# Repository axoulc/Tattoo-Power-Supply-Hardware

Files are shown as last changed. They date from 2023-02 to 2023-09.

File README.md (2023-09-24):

# Tattoo Power Supply Hardware

 

<p align="center">
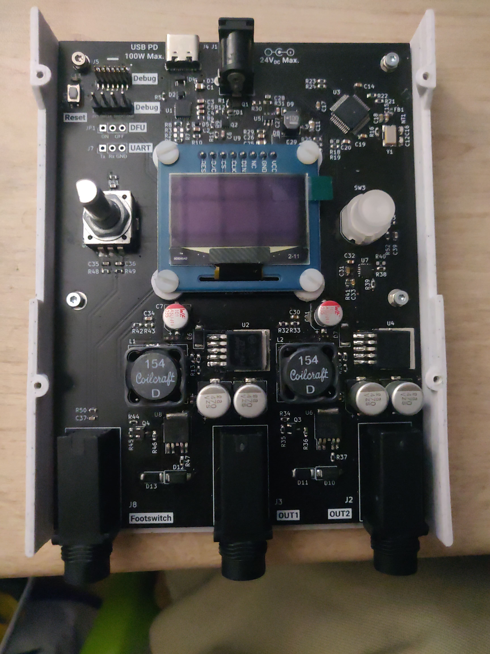
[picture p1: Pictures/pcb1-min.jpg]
    
</p>

This is an open source project for a tattoo power supply circuit board. The circuit board is designed to provide power to tattoo machines, allowing artists to control the voltage and frequency of their machines for precise and consistent results.

# Features

- Dual channel power supply
- Each channel can provide up to 20V and 3A
- 1 footswitch input and 1 handswitch input
- Adjustable voltage and frequency controls
- Compatible with most tattoo machines
- OLED display for easy monitoring of voltage and frequency
- Overload protection for safety
- USB-C Power Delivery up to 100W
- DC Jack input up to 24V

# Getting Started

## PCB

To get started with this project, you will need at least KiCAD 7. You can download KiCAD from the [KiCAD website](https://kicad.org/). You will find gerber files in each release, which you can use to order PCBs from a PCB manufacturer. Every files will be available in the PCB folder. For components, you can use the BOM file to order them from a distributor `Tattoo_Supply_bom_Vx.x.csv`.

## Case

<p align="center">
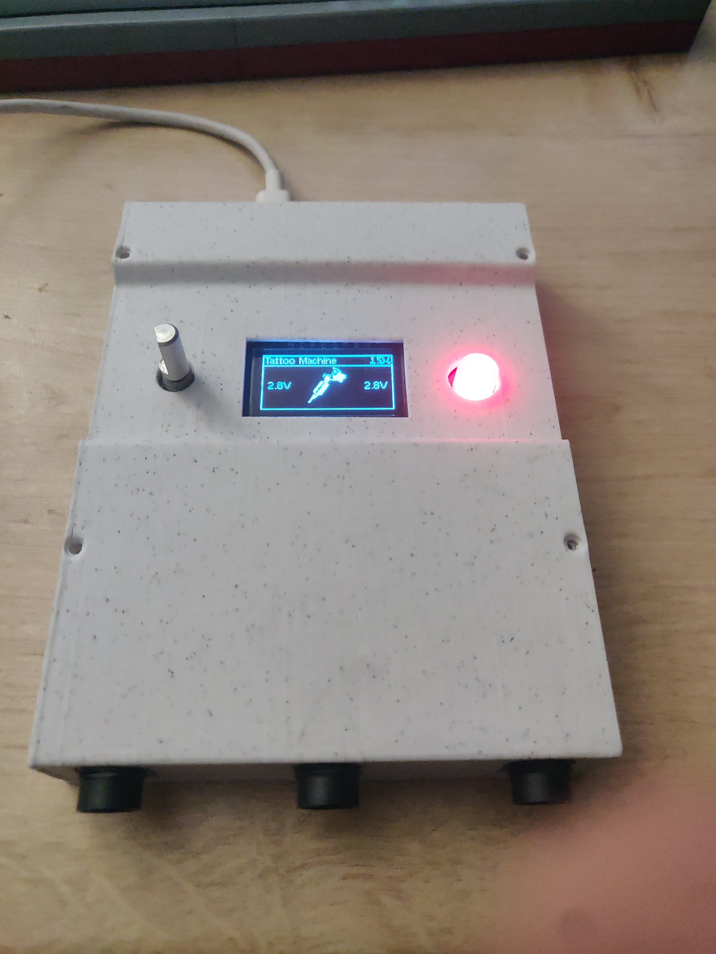
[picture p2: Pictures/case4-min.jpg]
    
</p>

The case is designed with FreeCAD. In `Case` folder, you will find `.FCStd` files which are source files for FreeCAD and `.3mf` files which are 3D printer ready. The shapes of the case are very simple, if you're 3D designer, make it prettier !

# License

This project is licensed under the CERN Open Hardware Licence Version 2 - Permissive. See the LICENSE file for more information.

# Contact

If you have any questions or feedback about this project, please feel free to contact the project maintainer in issue section.

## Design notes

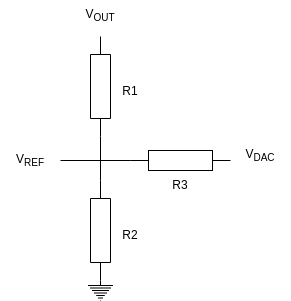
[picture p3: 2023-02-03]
PCB/notebook/img/smps_feedback.drawio.png

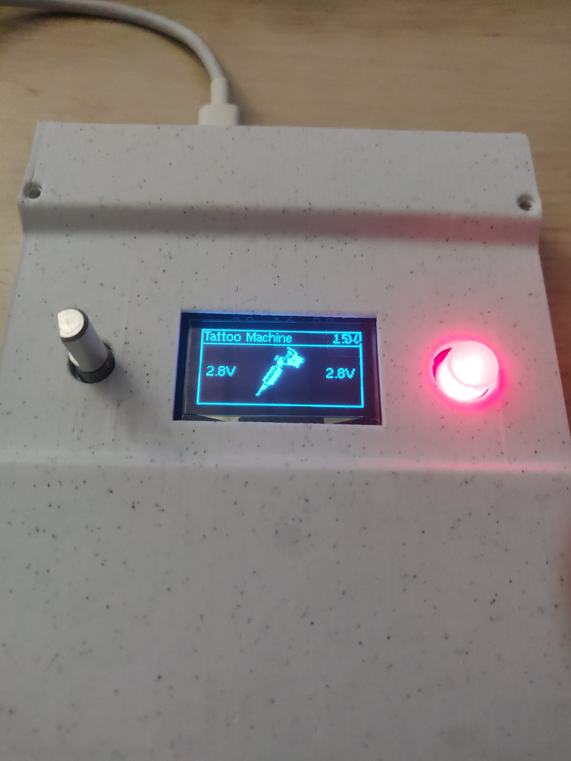
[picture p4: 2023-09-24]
Pictures/case3-min.jpg

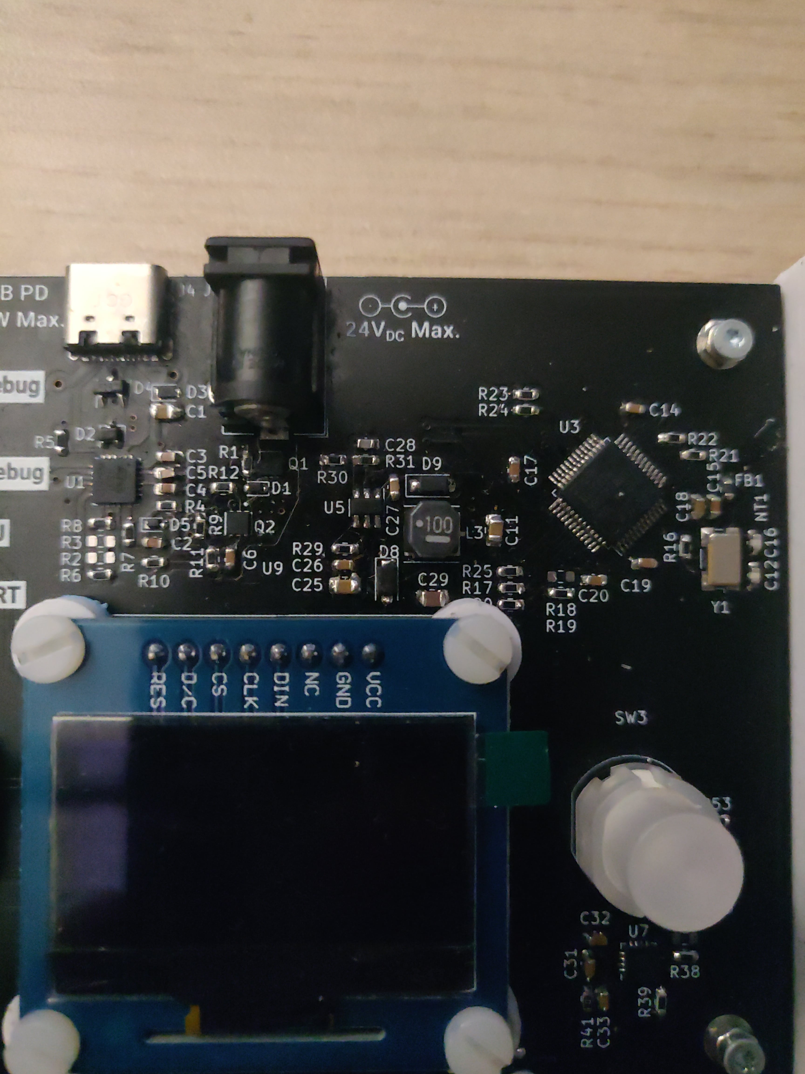
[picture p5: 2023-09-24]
Pictures/pcb3-min.jpg

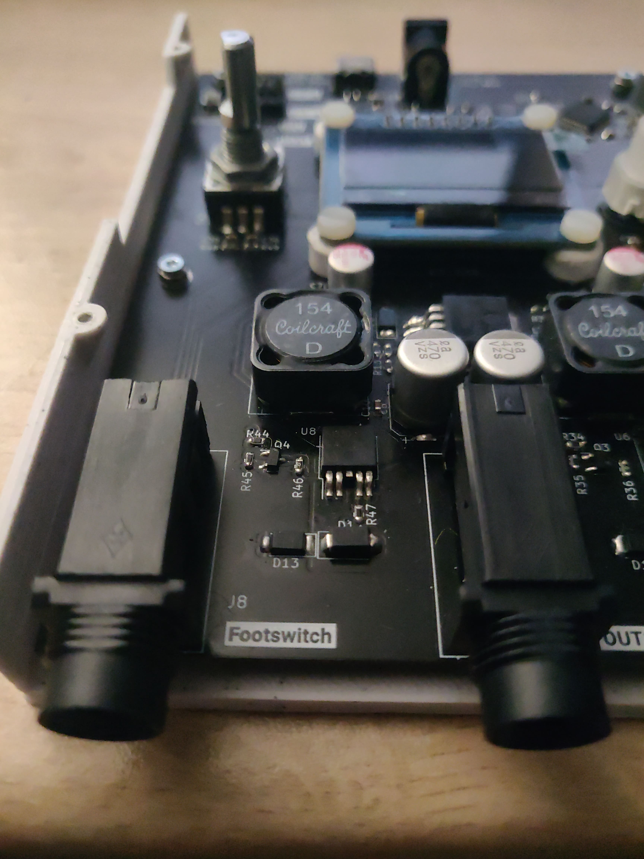
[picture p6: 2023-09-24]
Pictures/pcb2-min.jpg

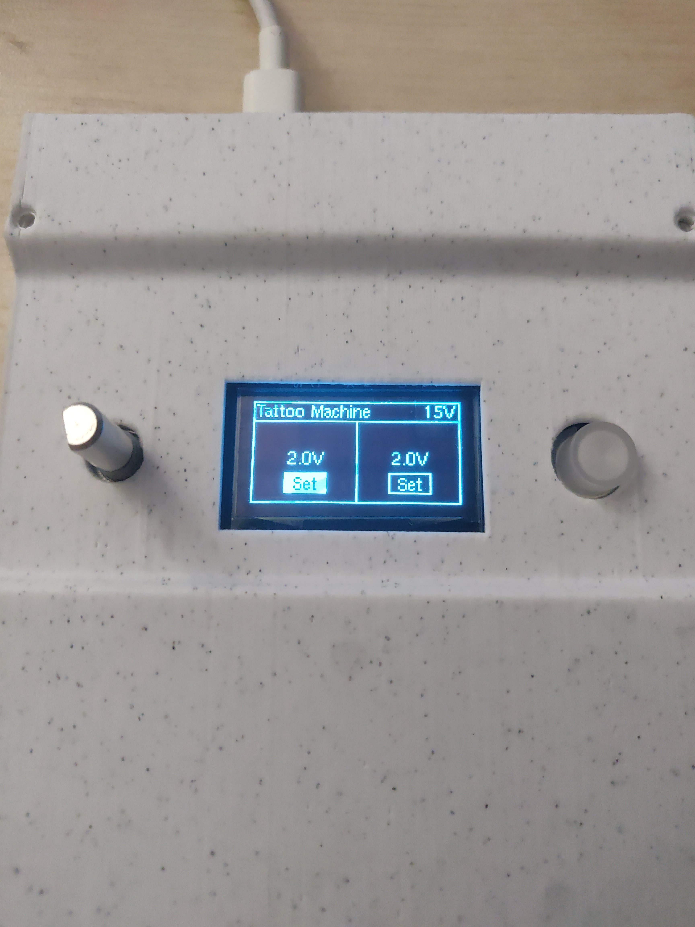
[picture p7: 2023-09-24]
Pictures/case2-min.jpg

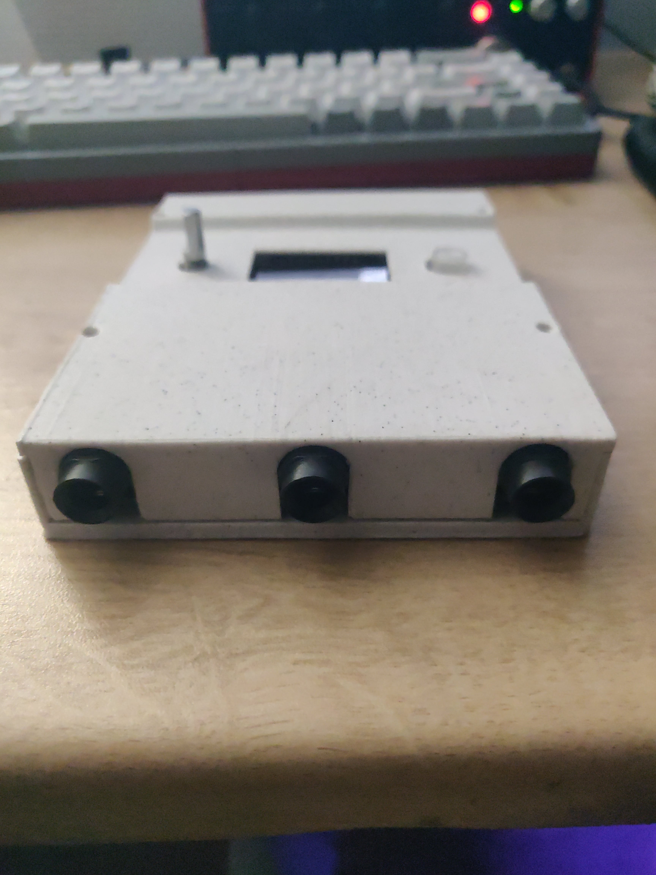
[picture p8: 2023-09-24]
Pictures/case1-min.jpg

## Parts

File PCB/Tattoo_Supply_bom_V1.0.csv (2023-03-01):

References | Value | Footprint | Quantity Per PCB | Manufacturer | MPN | Alt Manufacturer | Alt MPN
C12 C16 | 20p | C_0603_1608Metric | 2 | Kemet | C0603C200J5HACTU
C28 | 47p | C_0603_1608Metric | 1 | TDK | C1608C0G1H470J080AA
C18 C35 C36 C37 C38 C39 | 10n | C_0603_1608Metric | 6 | Murata | GCM188R71H103KA37J
C6 C13 C14 C17 C19 C20 C26 C27 C31 C33 | 100n | C_0603_1608Metric | 10 | TDK | CGA3E2X7R1H104M080AA
C2 C3 C4 C5 C10 C15 C24 C30 C34 | 1u | C_0603_1608Metric | 9 | TDK | CGA3E1X7R1V105K080AC
C32 | 1.5u | C_0603_1608Metric | 1 | TDK | C1608X7R1A155K080AC
C1 C11 C25 | 4.7u | C_0805_2012Metric | 3 | Murata | GRM219R6YA475KA73D
C29 | 22u | C_0805_2012Metric | 1 | Murata | GRM21BC81C226ME44L
C7 C21 | 100u/35V | CP_Elec_6.3x7.7 | 2 | Wurth Elektronik | 865080545012
C8 C9 C22 C23 | 470u/35V | CP_Elec_8x10 | 4 | United Chemi-Con | EMZS350ARA471MHA0G
D9 | 1N4148W | D_SOD-123 | 1 | Diodes Incorporated | 1N4148W-7-F
D10 D12 | 1SMA5936BT3G | D_SMA | 2 | Onsemi | 1SMA5936BT3G
D1 | BZX585-B10 | D_SOD-523 | 1 | Nexperia | BZX585-B10,135
D3 | ESDA25P35 | D_0603_1608Metric | 1 | STMicroelectronics | ESDA25P35-1U1M
D2 | ESDA25W | SOT-323_SC-70 | 1 | STMicroelectronics | ESDA25W
D4 | PACDN042Y3R | SOT-23-3 | 1 | Onsemi | PACDN042Y3R
D6 D7 | PMEG4050EP,115 | D_SOD-128 | 2 | Nexperia | PMEG4050EP,115
D8 | PMEG6010ER,115 | D_SOD-123F | 1 | Nexperia | PMEG6010ER,115
D5 | RB501SM-30FHT2R | D_SOD-523 | 1 | ROHM | RB501SM-30FHT2R
D11 D13 | RF202LAM2STR | D_SOD-128 | 2 | ROHM | RF202LAM2STR
FB1 | 600/100MHz | R_0603_1608Metric | 1 | Wurth Elektronik | 742792651
J1 | Barrel_Jack_Switch | BarrelJack_CUI_PJ-102AH_Horizontal | 1 | CUI Devices | PJ-102A
J5 | Conn_ST_STDC14 | PinSocket_2x07_P1.27mm_Vertical_SMD | 1 | Amphenol FCI | 20021121-00014C1LF
J2 J3 J8 | Out_{1} Out_{2} Footswitch | MJ63022A | 3 | CUI Devices | MJ-63022A
J4 | USB_C_Receptacle_USB2.0 | USB_C_Receptacle_GCT_USB4105-xx-A_16P_TopMnt_Horizontal | 1 | GCT | USB4105-GF-A
L1 L2 | MSS1583-154KED | MSS1583 | 2 | Coilcraft | MSS1583-154KED
L3 | NRS5040T100MMGJ | L_Taiyo-Yuden_NR-50xx | 1 | Taiyo Yuden | NRS5040T100MMGJ
Q3 Q4 | 2N7002 | SOT-23 | 2 | Nexperia | 2N7002NXAKR
Q2 | SSM6J507NU | TRANS_SSM6J507NU,LF | 1 | Toshiba | SSM6J507NU,LF
Q1 | SiA441DJ | Vishay_PowerPAK_SC70-6L_Single | 1 | Vishay Semiconductors | SIA441DJ-T1-GE3
R36 R46 | 0 | R_0603_1608Metric | 2 | Panasonic | ERJ-3GEY0R00V
R23 R24 | 20 | R_0603_1608Metric | 2 | Panasonic | ERJ-3EKF20R0V
R34 R44 | 22 | R_0603_1608Metric | 2 | Panasonic | ERJ-3EKF22R0V
R11 | 100 | R_0603_1608Metric | 1 | Panasonic | ERJ-3EKF1000V
R4 | 470 | R_0603_1608Metric | 1 | Panasonic | ERJ-3EKF4700V
R16 | 953 | R_0603_1608Metric | 1 | Panasonic | ERJ-3EKF9530V
R7 R12 R14 R27 R37 R47 R53 | 1k | R_0603_1608Metric | 7 | Panasonic | ERJ-3EKF1001V
R33 R43 | 1.62k | R_0603_1608Metric | 2 | Panasonic | ERJ-3EKF1621V
R15 R28 | 1.65k | R_0603_1608Metric | 2 | Panasonic | ERJ-3EKF1651V
R17 R20 | 4.7k | R_0603_1608Metric | 2 | Panasonic | ERJ-3EKF4701V
R13 R26 | 8.45k | R_0603_1608Metric | 2 | Panasonic | ERJ-3EKF8451V
R21 R35 R38 R39 R41 R45 R48 R49 R50 R51 R52 | 10k | R_0603_1608Metric | 11 | Panasonic | ERJ-3EKF1002V
R32 R42 | 13.3k | R_0603_1608Metric | 2 | Panasonic | ERJ-3EKF1332V
R10 | 18k | R_0603_1608Metric | 1 | Panasonic | ERJ-3EKF1802V
R30 | 40.2k | R_0603_1608Metric | 1 | Panasonic | ERJ-3EKF4022V
R1 R5 R6 R8 R9 R18 R19 R22 R25 | 100k | R_0603_1608Metric | 9 | Panasonic | ERJ-3EKF1003V
R31 | 124k | R_0603_1608Metric | 1 | Panasonic | ERJ-3EKF1243V
R29 | 499k | R_0603_1608Metric | 1 | Panasonic | ERJ-3EKF4993V
SW3 | Handswitch W LED | D6RLxx | 1 | C&K | D6RLRDF1 LFS
SW1 | Reset | SW_SPST_EVQP2 | 1 | Panasonic | EVQ-P2602W
SW2 | RotaryEncoder_Switch | RotaryEncoder_Alps_EC11E-Switch_Vertical_H20mm | 1 | Bourns | PEC11R-4220F-S0024
U6 U8 | BTS6133D | TO-252-4 | 2 | Infineon | BTS6133D
U7 | DACx3202 | WQFN-16-1EP_3x3mm_P0.5mm_EP1.68x1.68mm | 1 | Texas Instruments | DAC63202RTER
U2 U4 | LM2576S-ADJ | TO-263-5_TabPin3 | 2 | Onsemi | LM2576D2T-ADJR4G
U5 | MP2456 | TSOT-23-6 | 1 | Monolithic Power Systems | MP2456GJ-Z
U9 | OLED_Waveshare | OLEDs_Waveshare_4SPI | 1 | 10451 | Waveshare | Waveshare | 9092
U3 | STM32F103C8Tx | LQFP-48_7x7mm_P0.5mm | 1 | STMicroelectronics | STM32F103C8T6
U1 | STUSB4500QTR | QFN-24-1EP_4x4mm_P0.5mm_EP2.7x2.7mm | 1 | STMicroelectronics | STUSB4500QTR
Y1 | ABM3B-8.000MHZ-B2-T | Crystal_SMD_Abracon_ABM3B-4Pin_5.0x3.2mm | 1 | Abracon | ABM3B-8.000MHZ-B2-T

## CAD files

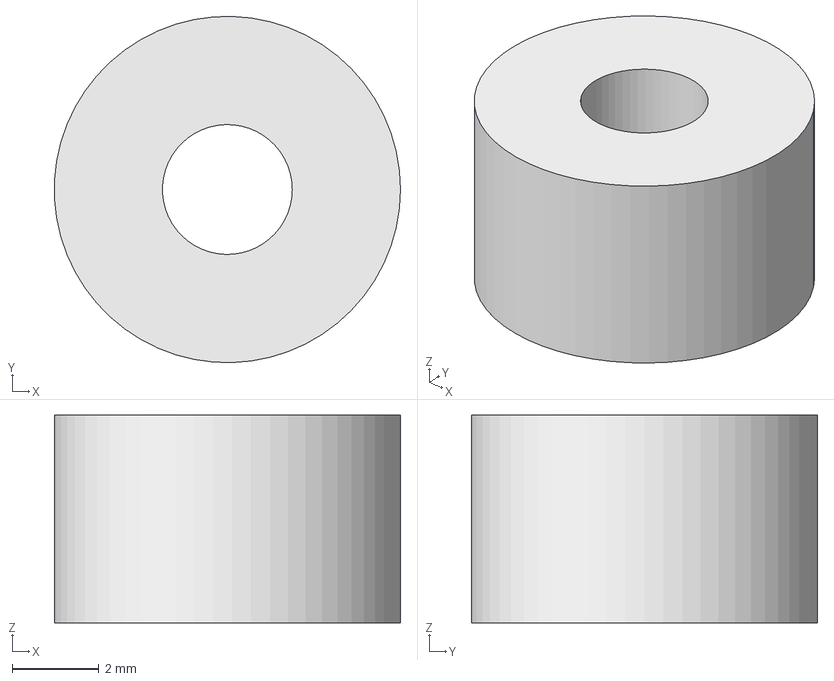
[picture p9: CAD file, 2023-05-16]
Case/oled_spacers.FCStd
7.99 x 8.00 x 4.80 mm

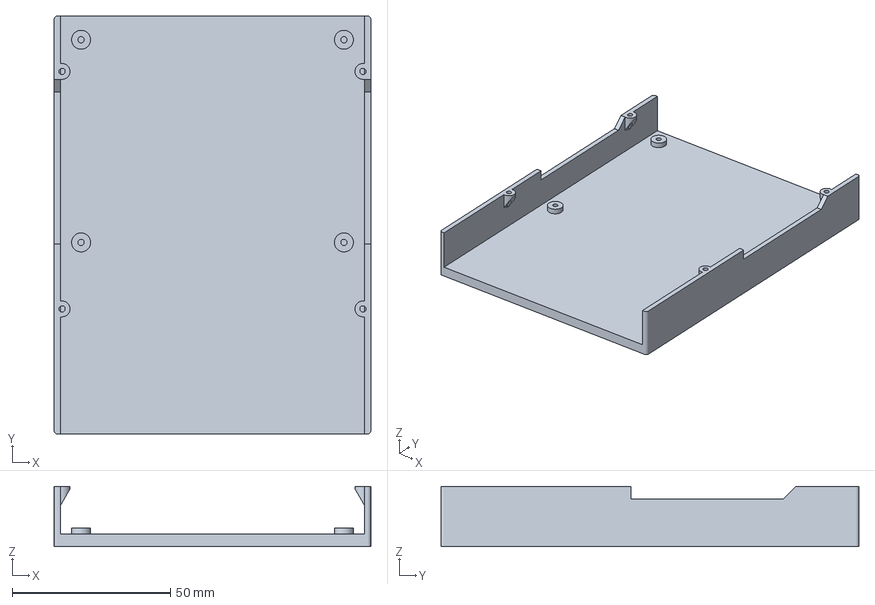
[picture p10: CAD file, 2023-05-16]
Case/Case_V1_bottom.3mf
100.0 x 132.0 x 19.0 mm

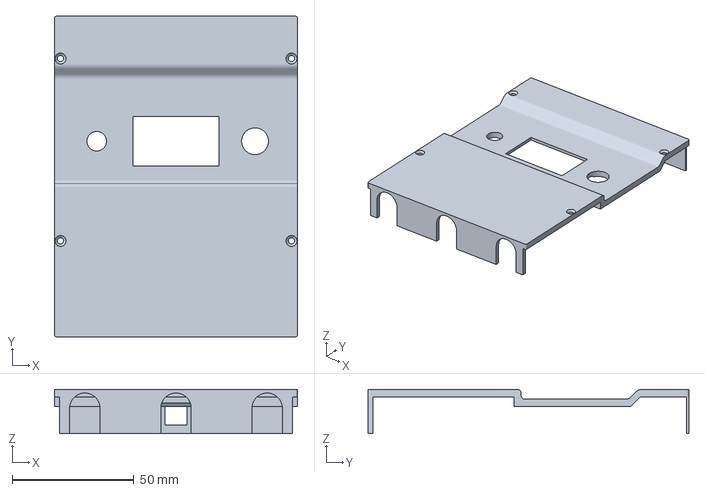
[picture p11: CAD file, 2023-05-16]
Case/Case_V1_top.3mf
100.0 x 132.0 x 18.1 mm

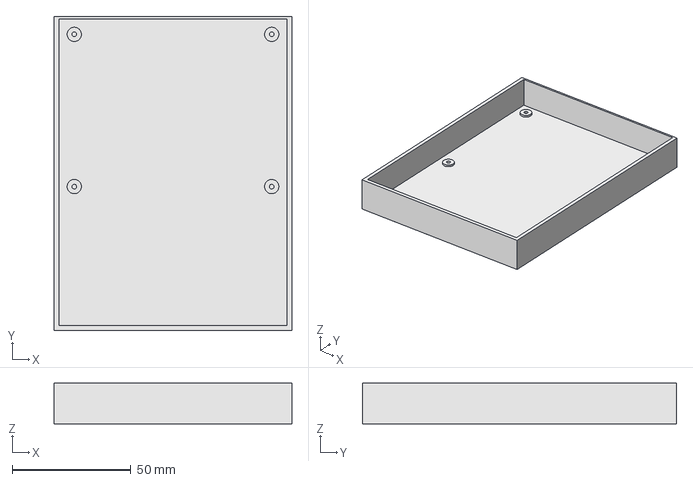
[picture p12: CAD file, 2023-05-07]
Case/Case_V1.0.FCStd
100.0 x 132.0 x 17.1 mm

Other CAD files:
Case/Oled_Spacers.3mf

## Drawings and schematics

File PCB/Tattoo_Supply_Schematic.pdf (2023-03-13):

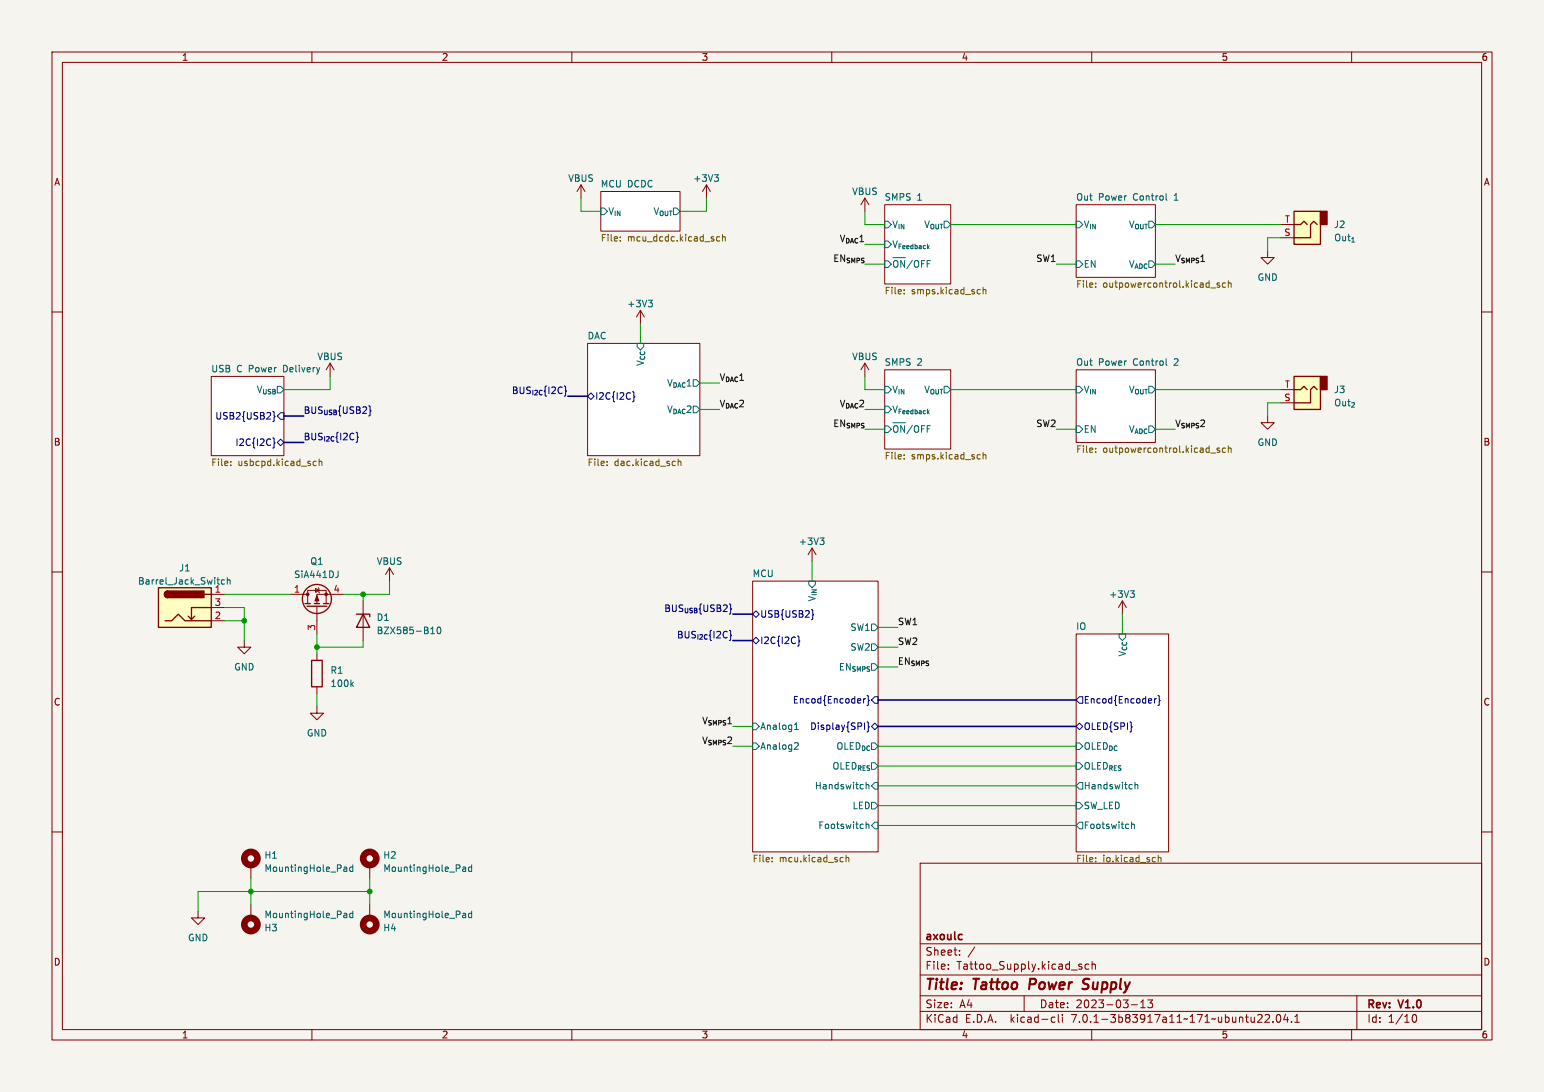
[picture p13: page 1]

~{ON}/OFF SMPS 1 File: smps.kicad_sch

VBUS
~{ON}/OFF SMPS 2 File: smps.kicad_sch
LED MCU

Encod{Encoder} V_{CC} Footswitch Handswitch OLED{SPI}

Id: 1/10 Title: Tattoo Power Supply

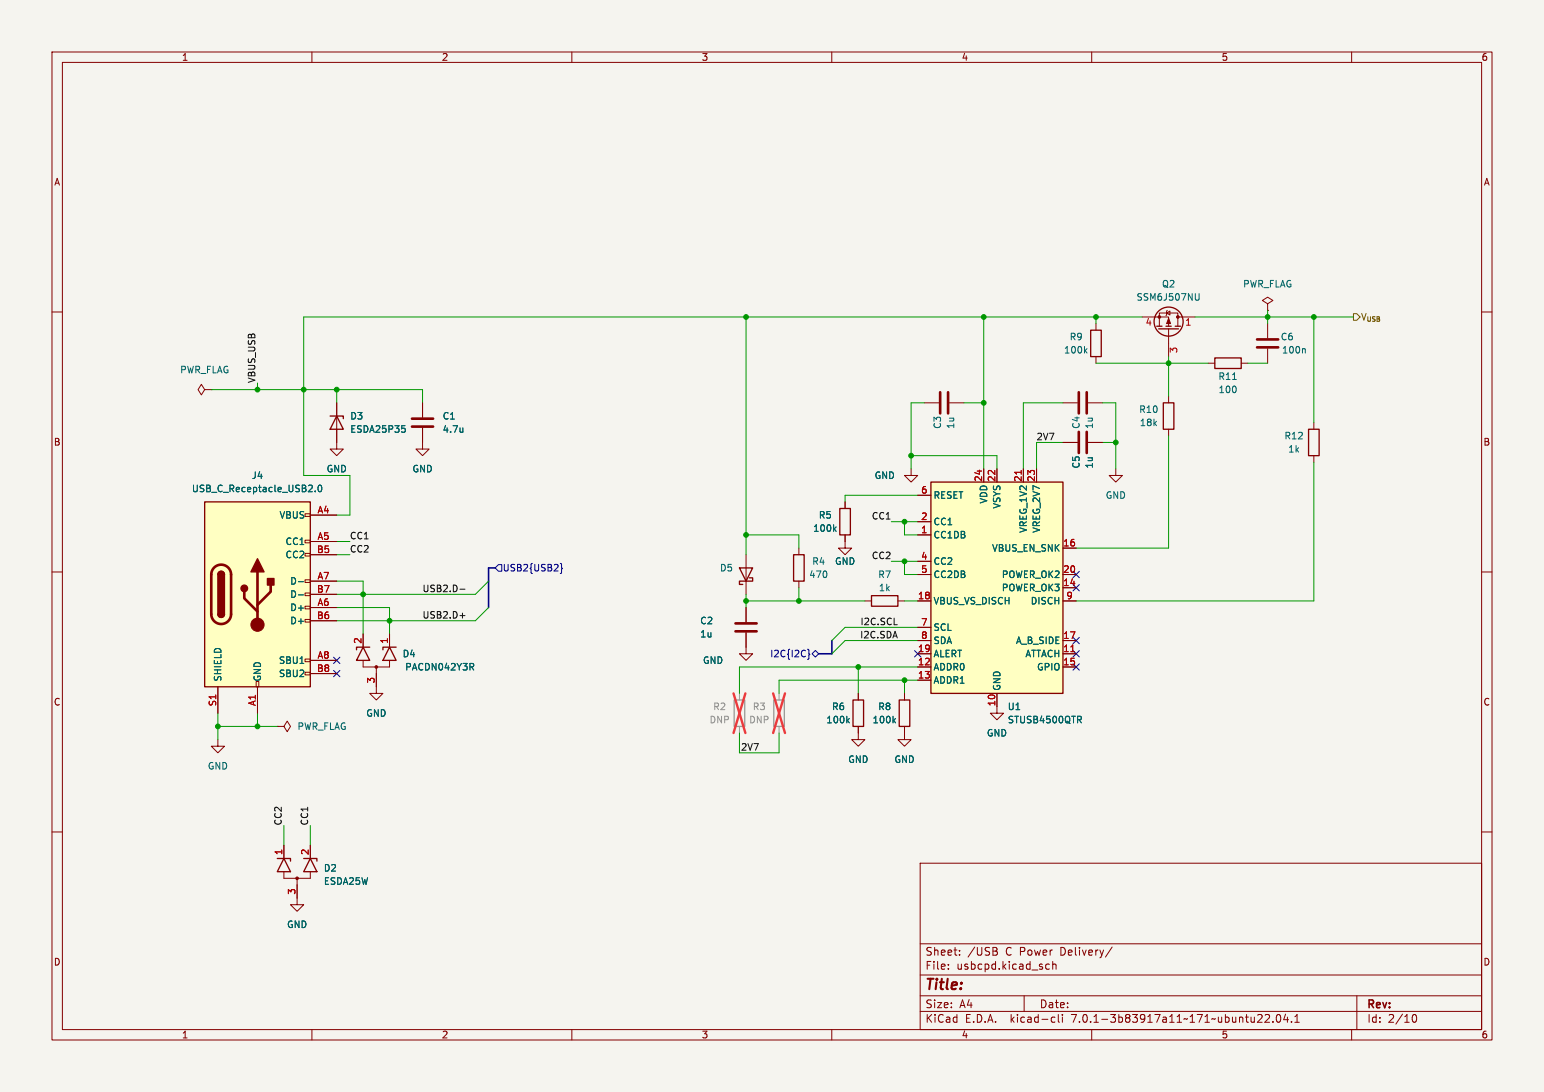
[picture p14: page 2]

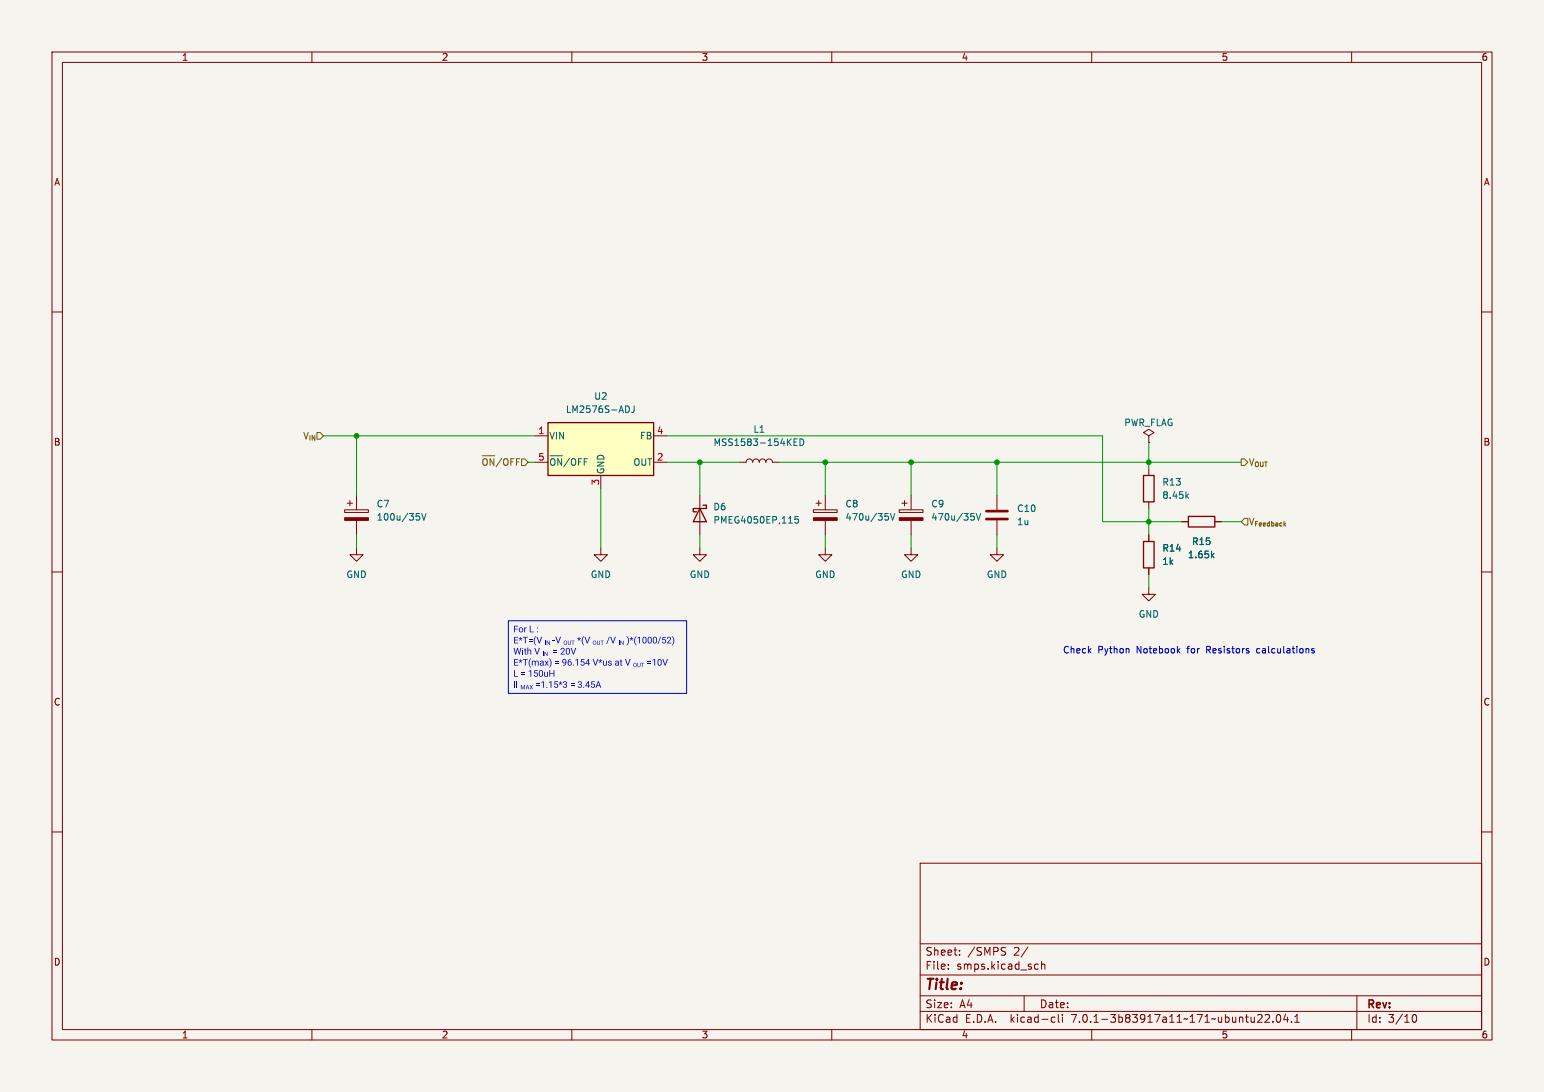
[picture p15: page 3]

Id: 3/10 Title: File: smps.kicad_sch Sheet: /SMPS 2/ C9

E*T(max) = 96.154 V*us at V _{OUT} =10V

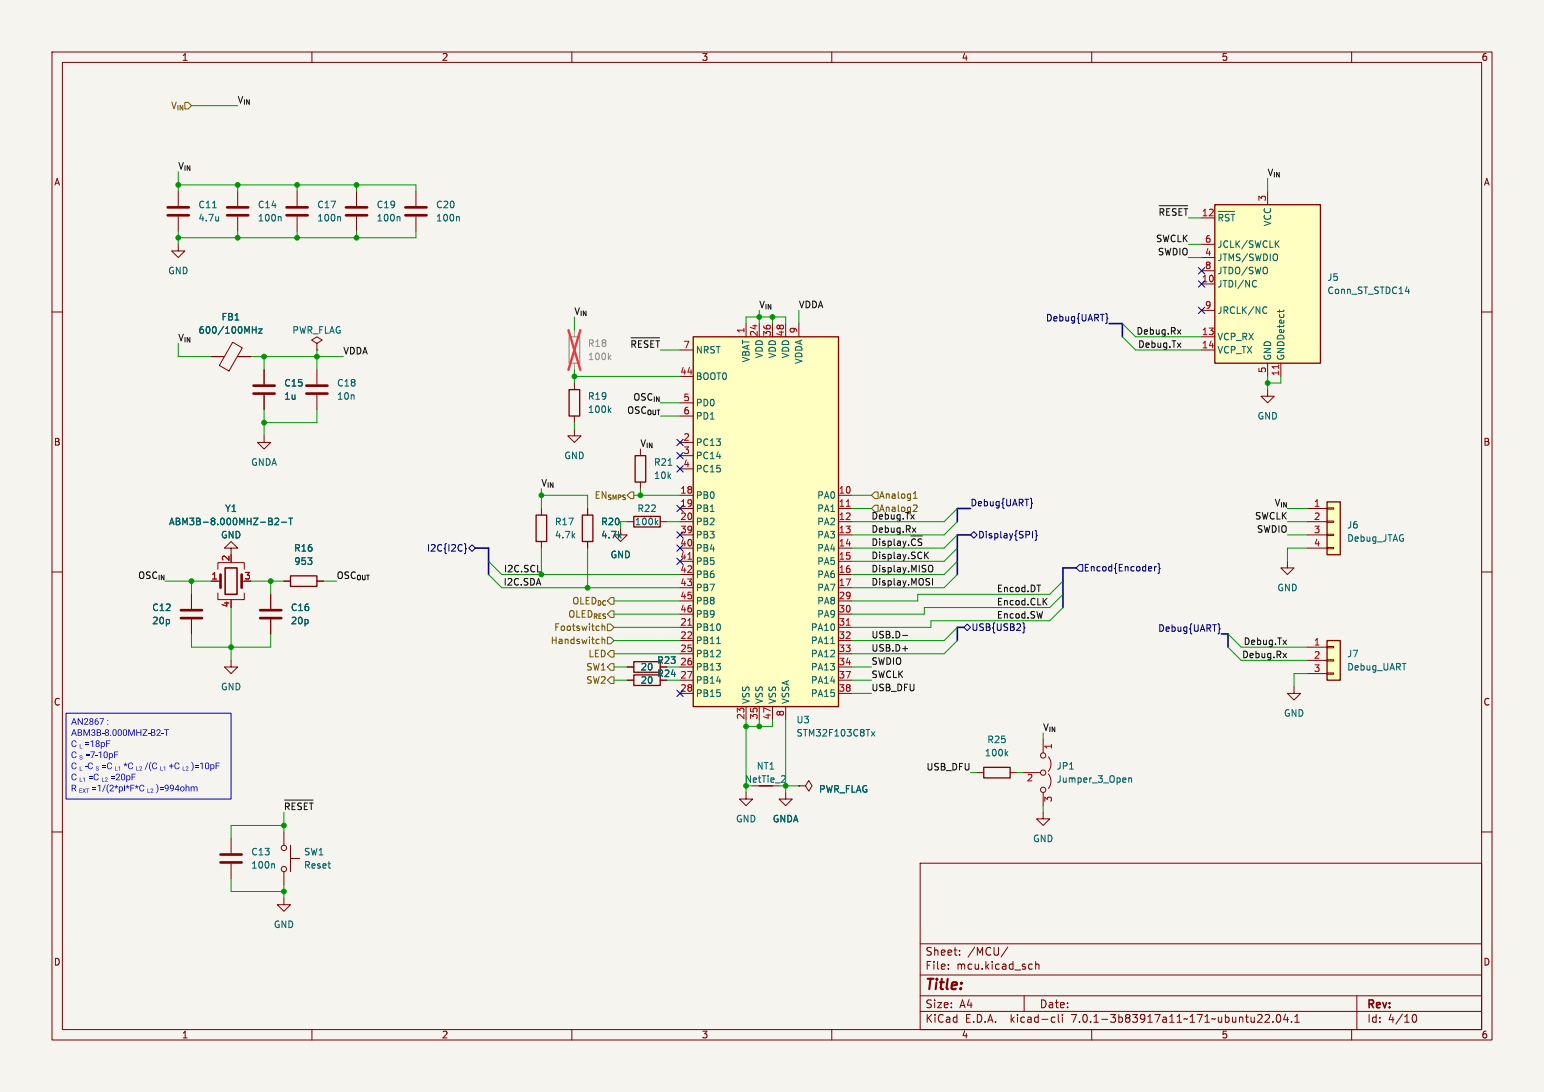
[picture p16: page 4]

1 PA0 10 PA1 11 PA2 12 PA3 13 PA4 14 PA5 15 PA6 16 PA7 17 PB0 18 PB1 19 PC13 2 PB2 20 PB10 21 PB11 22 VSS 23 VDD 24 PB12 25 PB13 26 PB14 27 PB15 28 PA8 29 PC14 3 PA9 30 PA10 31 PA11 32 PA12 33 PA13 34 VSS 35 VDD 36 PA14 37 PA15 38 PB3 39 PC15 4 PB4 40 PB5 41 PB6 42 PB7 43 BOOT0 44 PB8 45 PB9 46 VSS 47 VDD 48 PD0 5 PD1 6 NRST 7 VSSA

Id: 4/10 Title: File: mcu.kicad_sch Sheet: /MCU/ R23

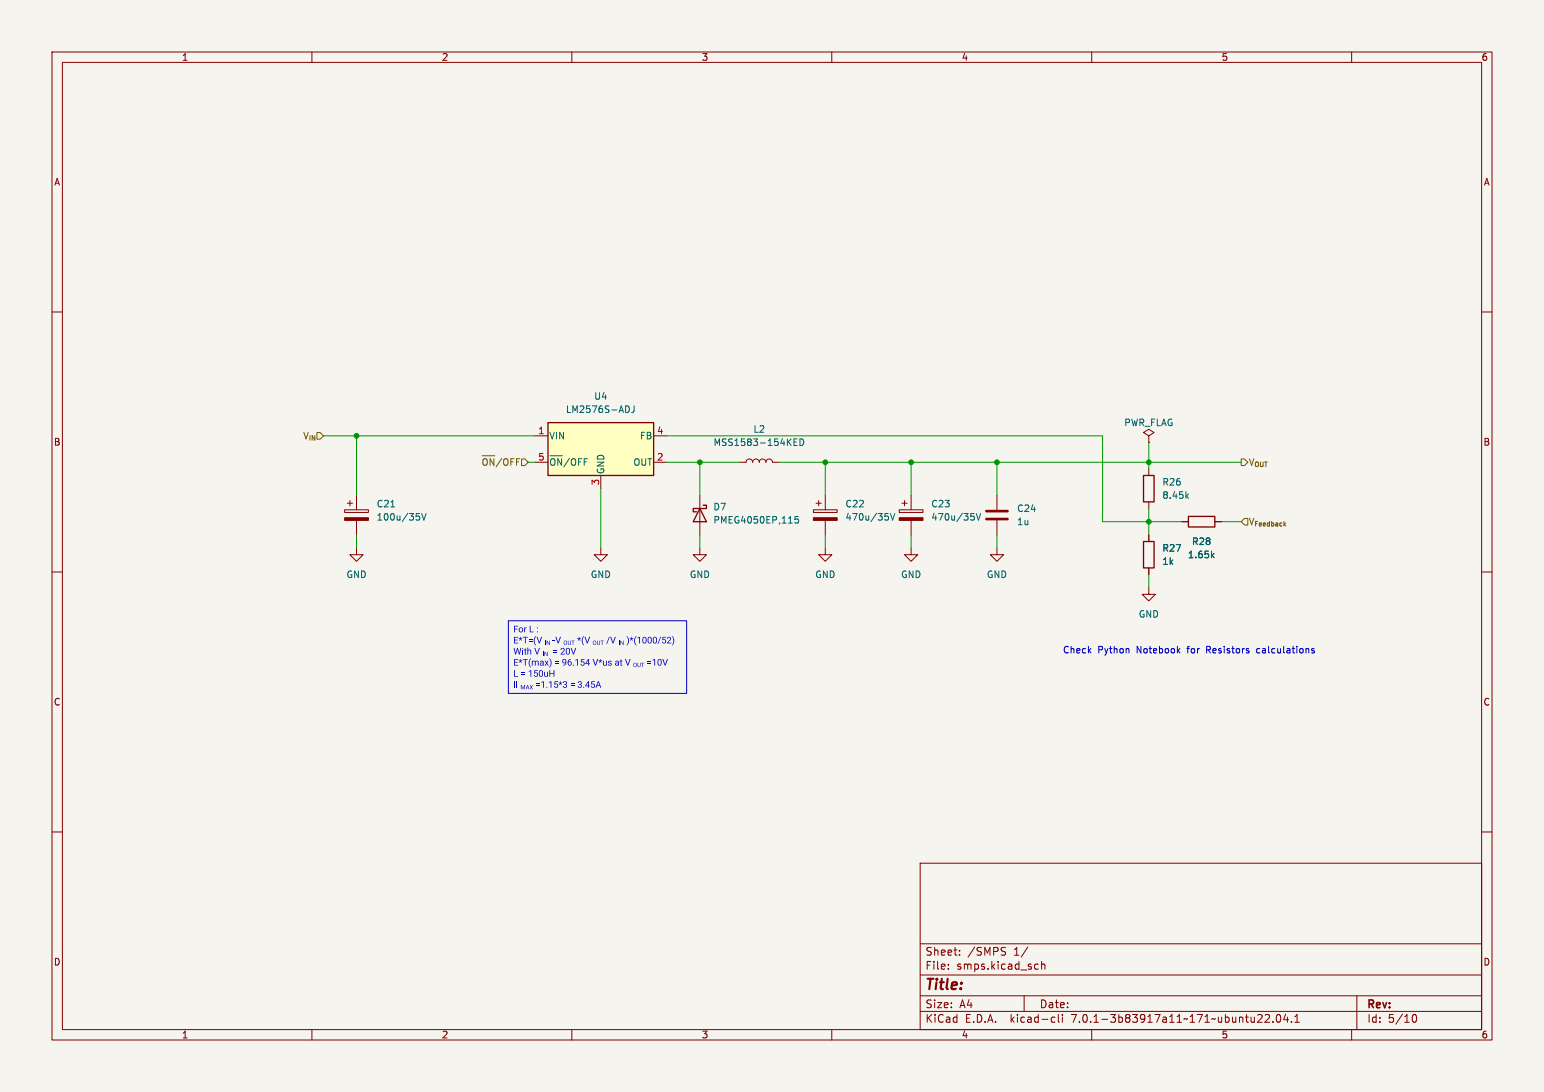
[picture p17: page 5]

Id: 5/10 Title: File: smps.kicad_sch Sheet: /SMPS 1/ C22

E*T(max) = 96.154 V*us at V _{OUT} =10V

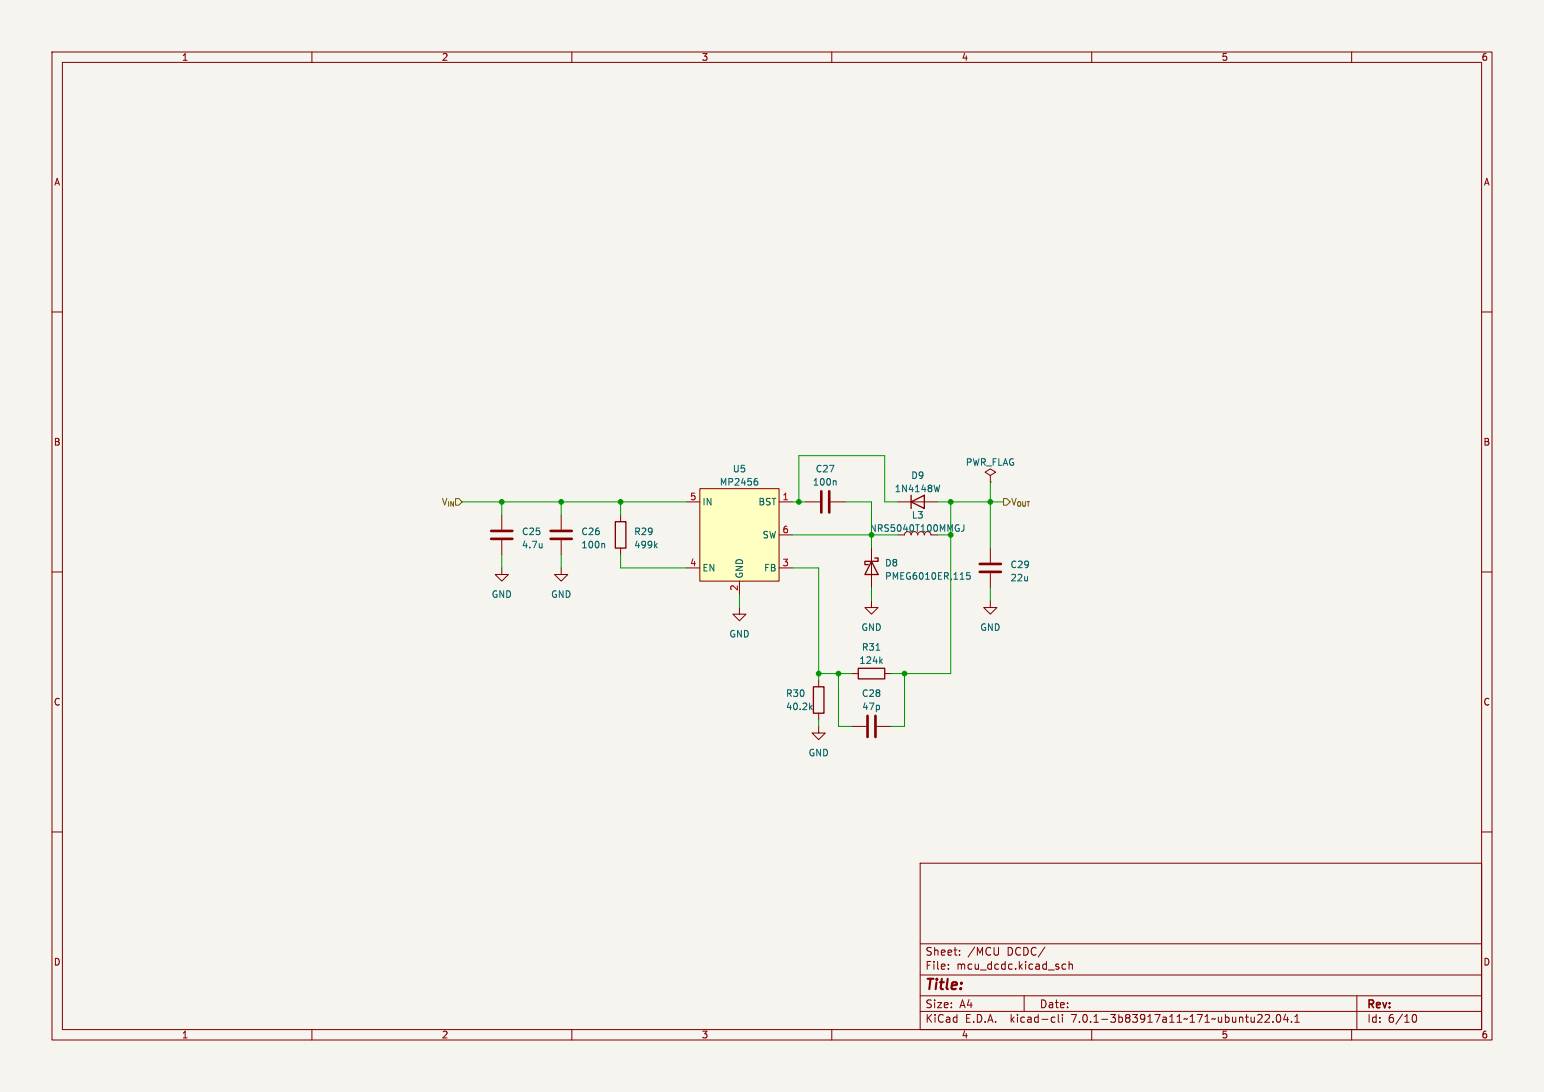
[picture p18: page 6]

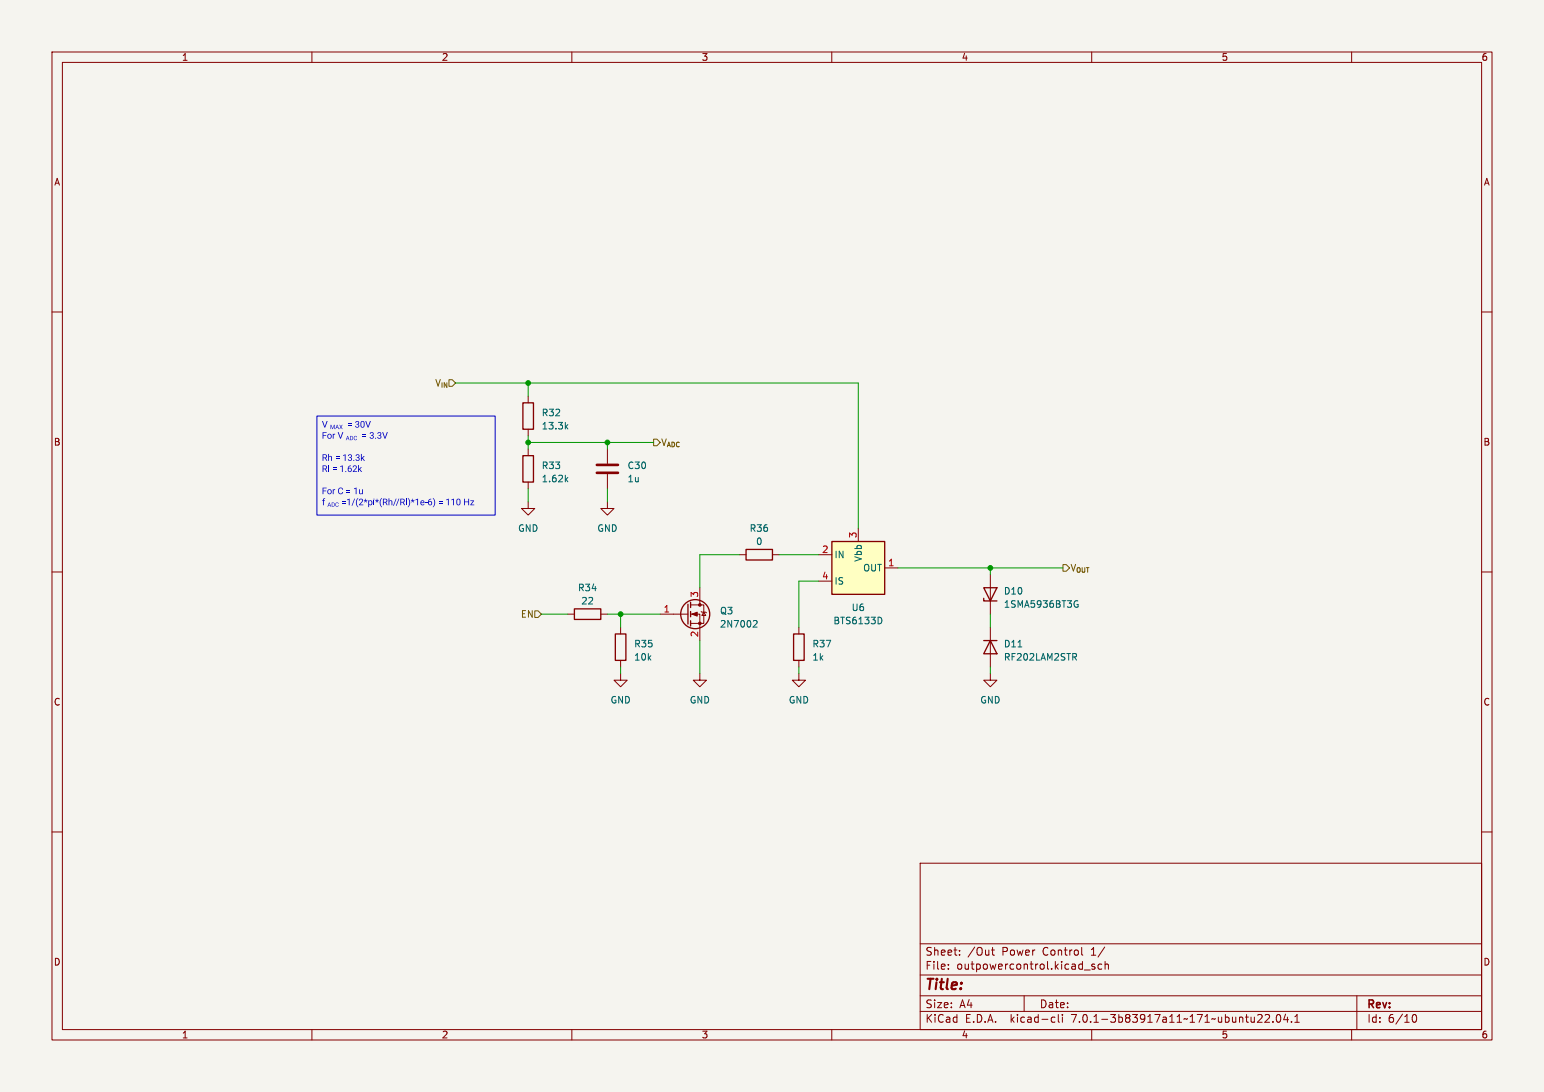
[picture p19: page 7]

V _{MAX} = 30V
For V _{ADC} = 3.3V Rh= 13.3k Rl = 1.62k For C = 1u

f _{ADC} =1/(2*pi*(Rh//Rl)*1e-6) = 110 Hz

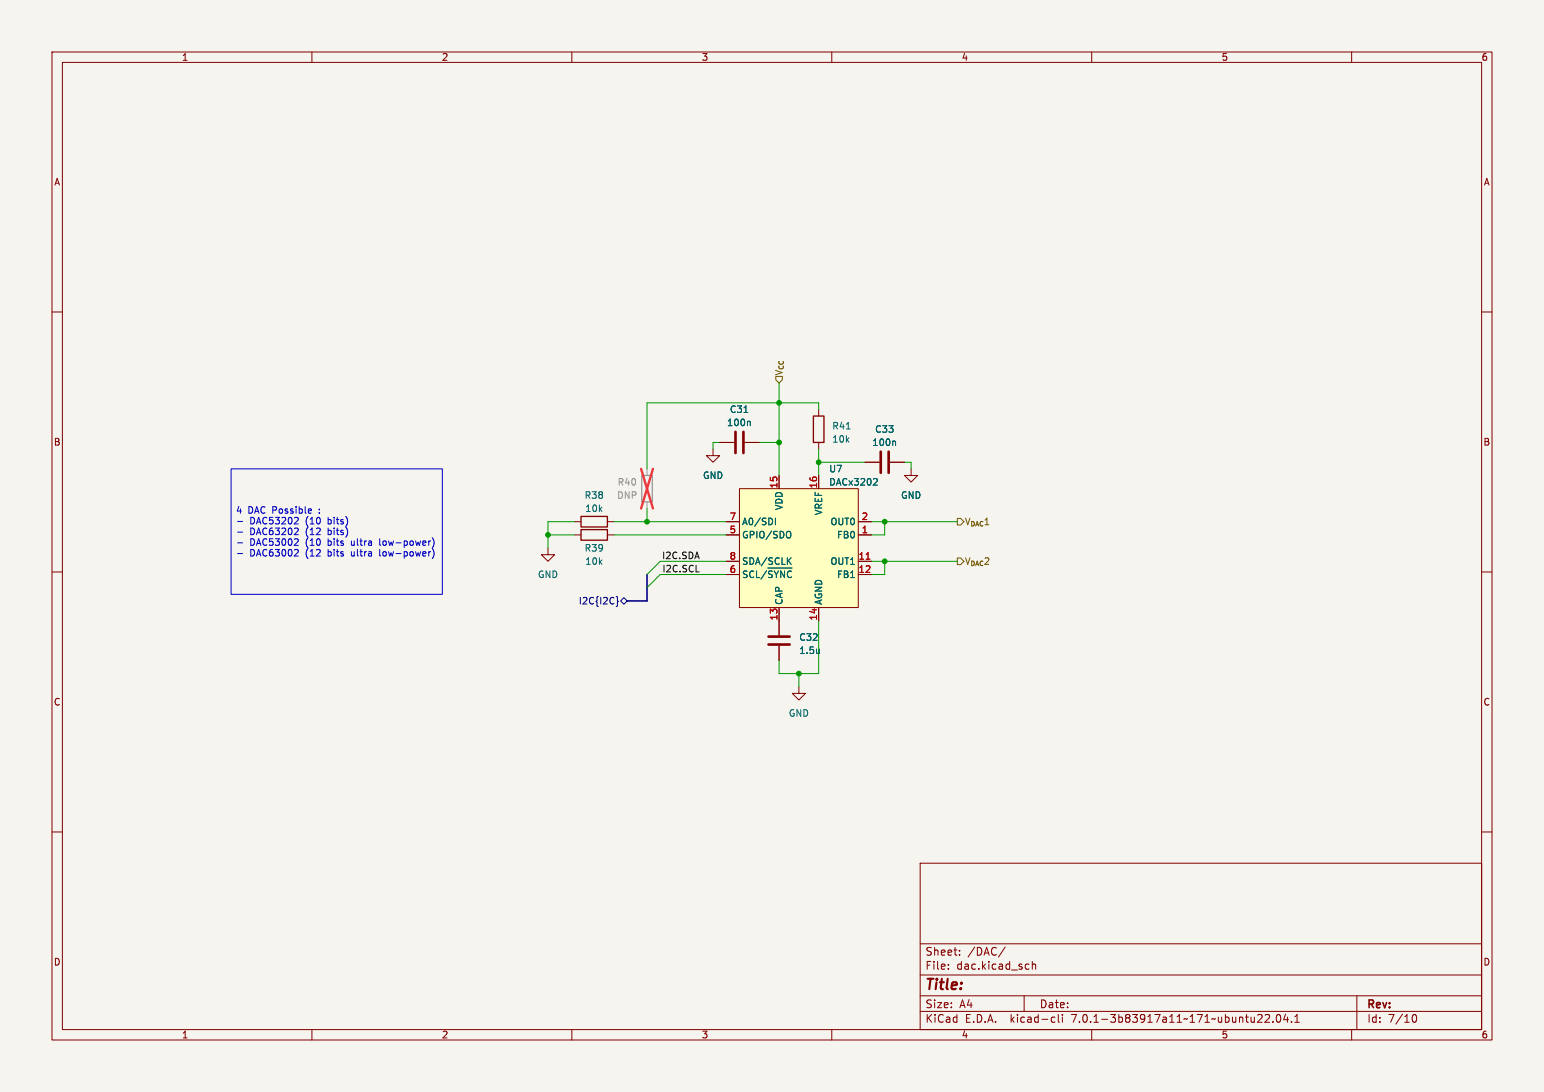
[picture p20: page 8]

- DAC63202 (12 bits)
- DAC53002 (10 bits ultra low-power)

Id: 7/10 Title: File: dac.kicad_sch Sheet: /DAC/

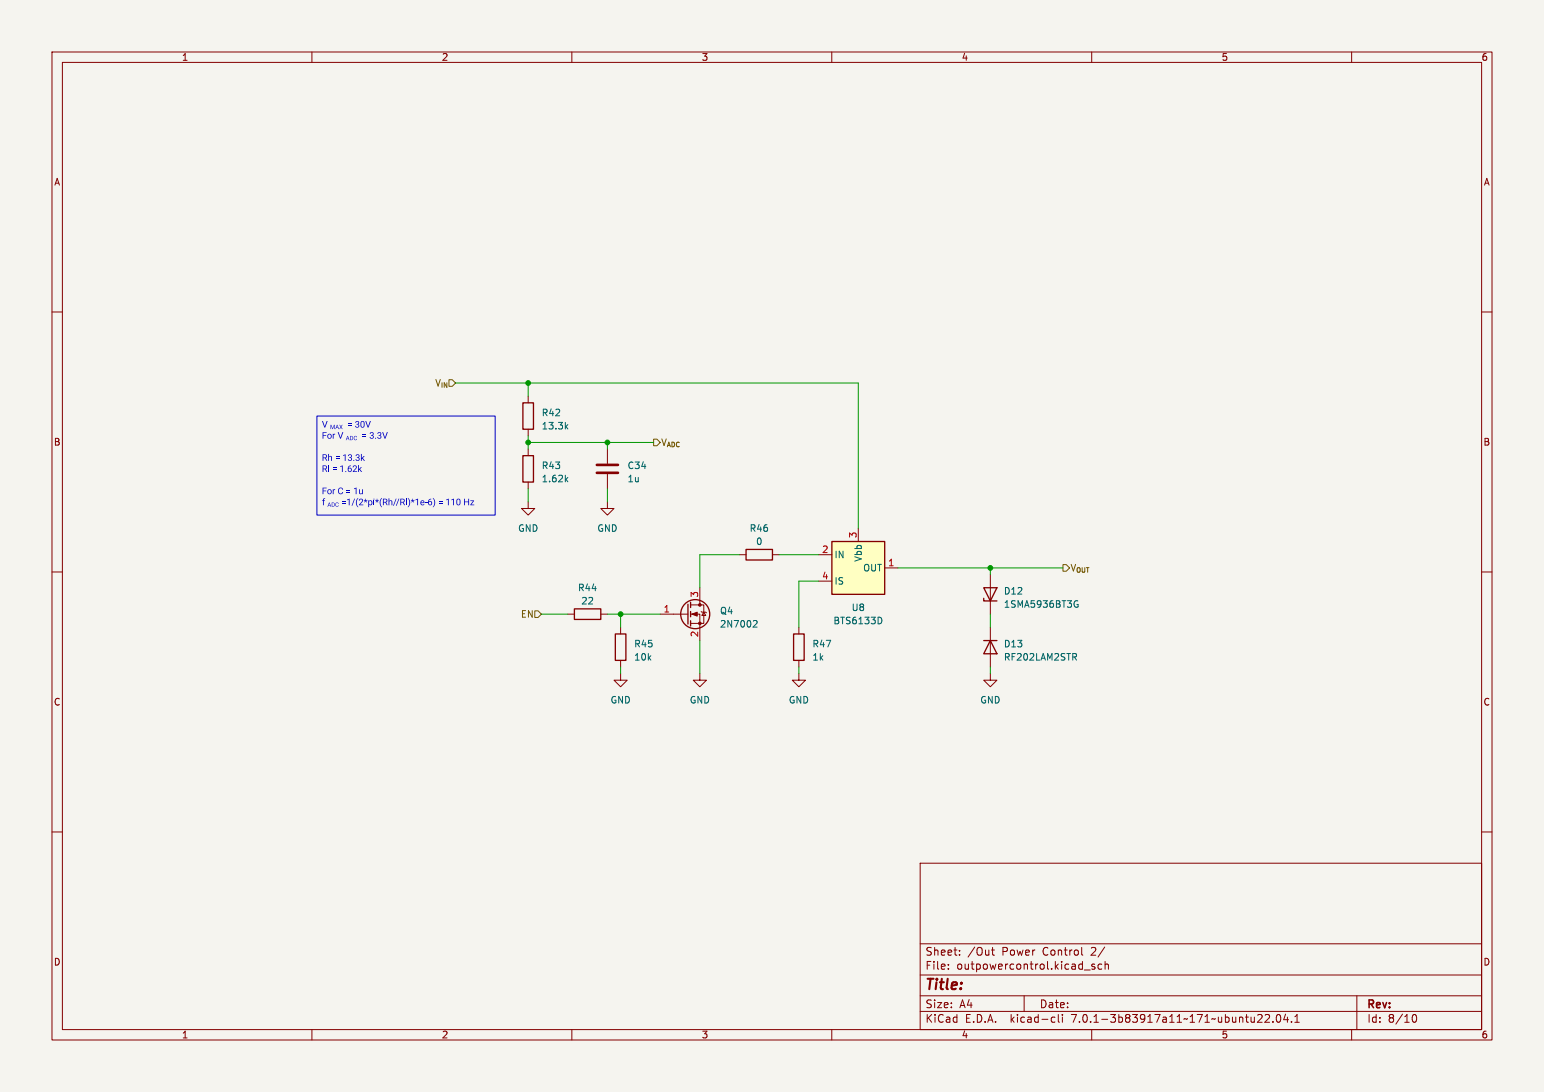
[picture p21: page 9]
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

f _{ADC} =1/(2*pi*(Rh//Rl)*1e-6) = 110 Hz

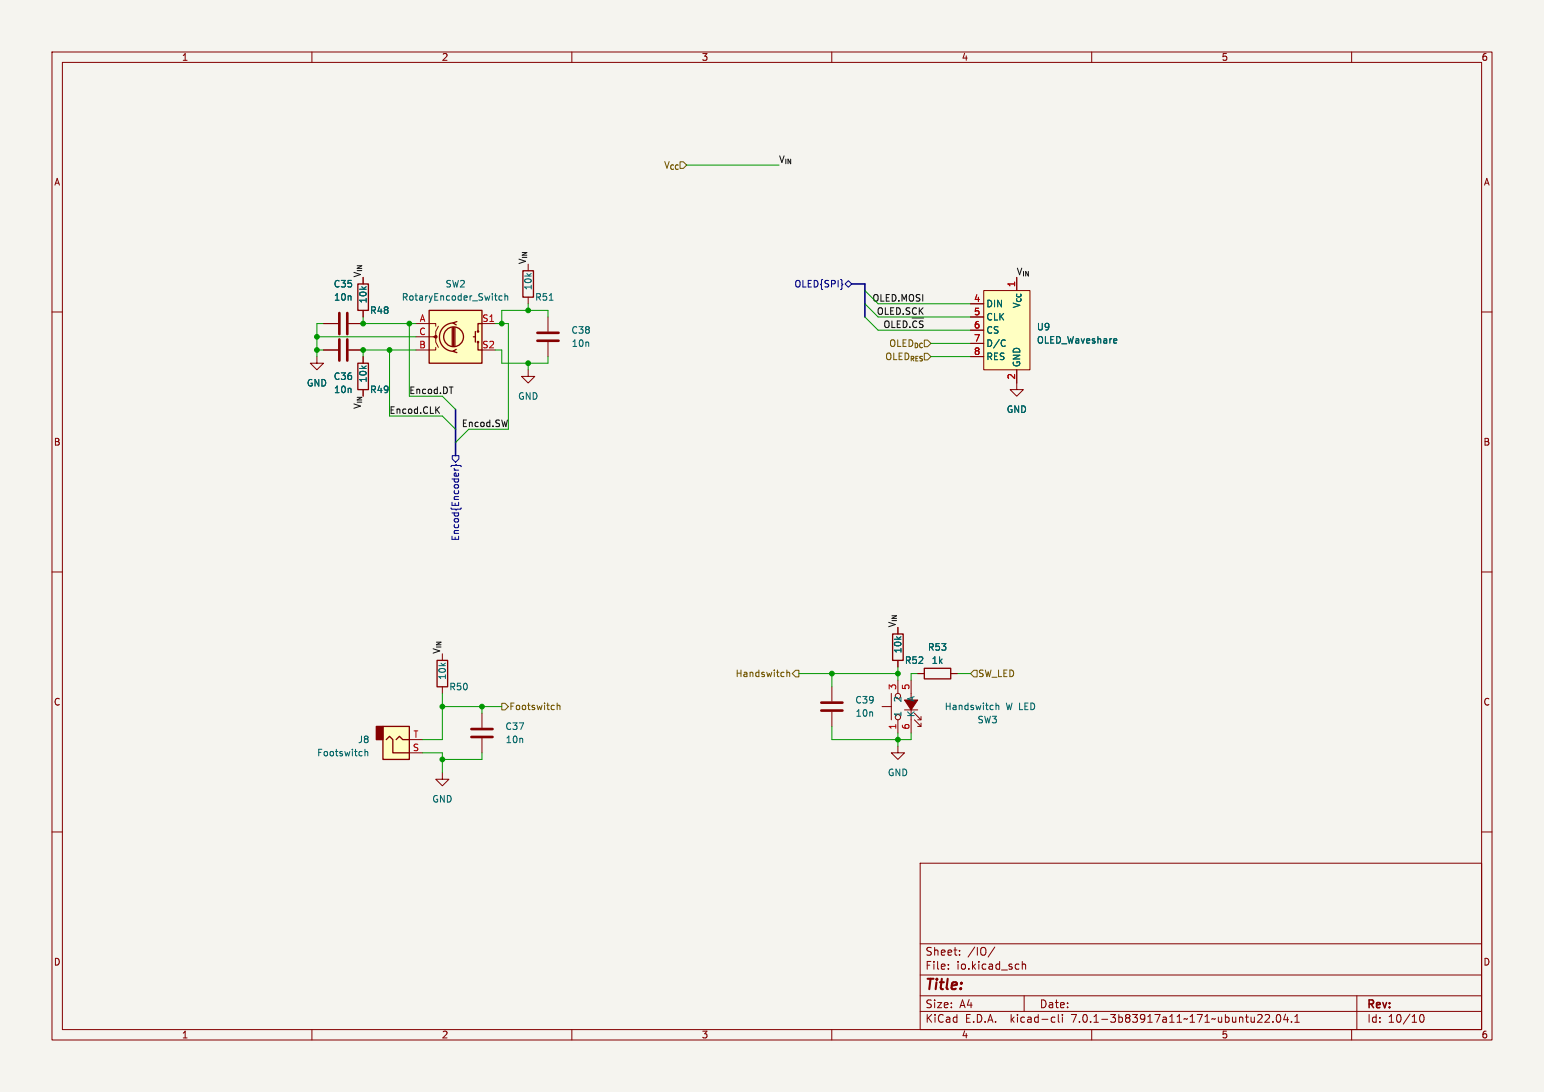
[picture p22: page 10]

2 DIN 4 CLK 5 CS 6 D/C 7 RES 8 U9 OLED_Waveshare R50 10k Encod{Encoder} Footswitch OLED_{DC} Handswitch OLED_{RES}

2 DIN 4 CLK 5 CS 6 D/C 7 RES 8 R53 R52 1k 10k

Id: 10/10 Title: File: io.kicad_sch Sheet: /IO/

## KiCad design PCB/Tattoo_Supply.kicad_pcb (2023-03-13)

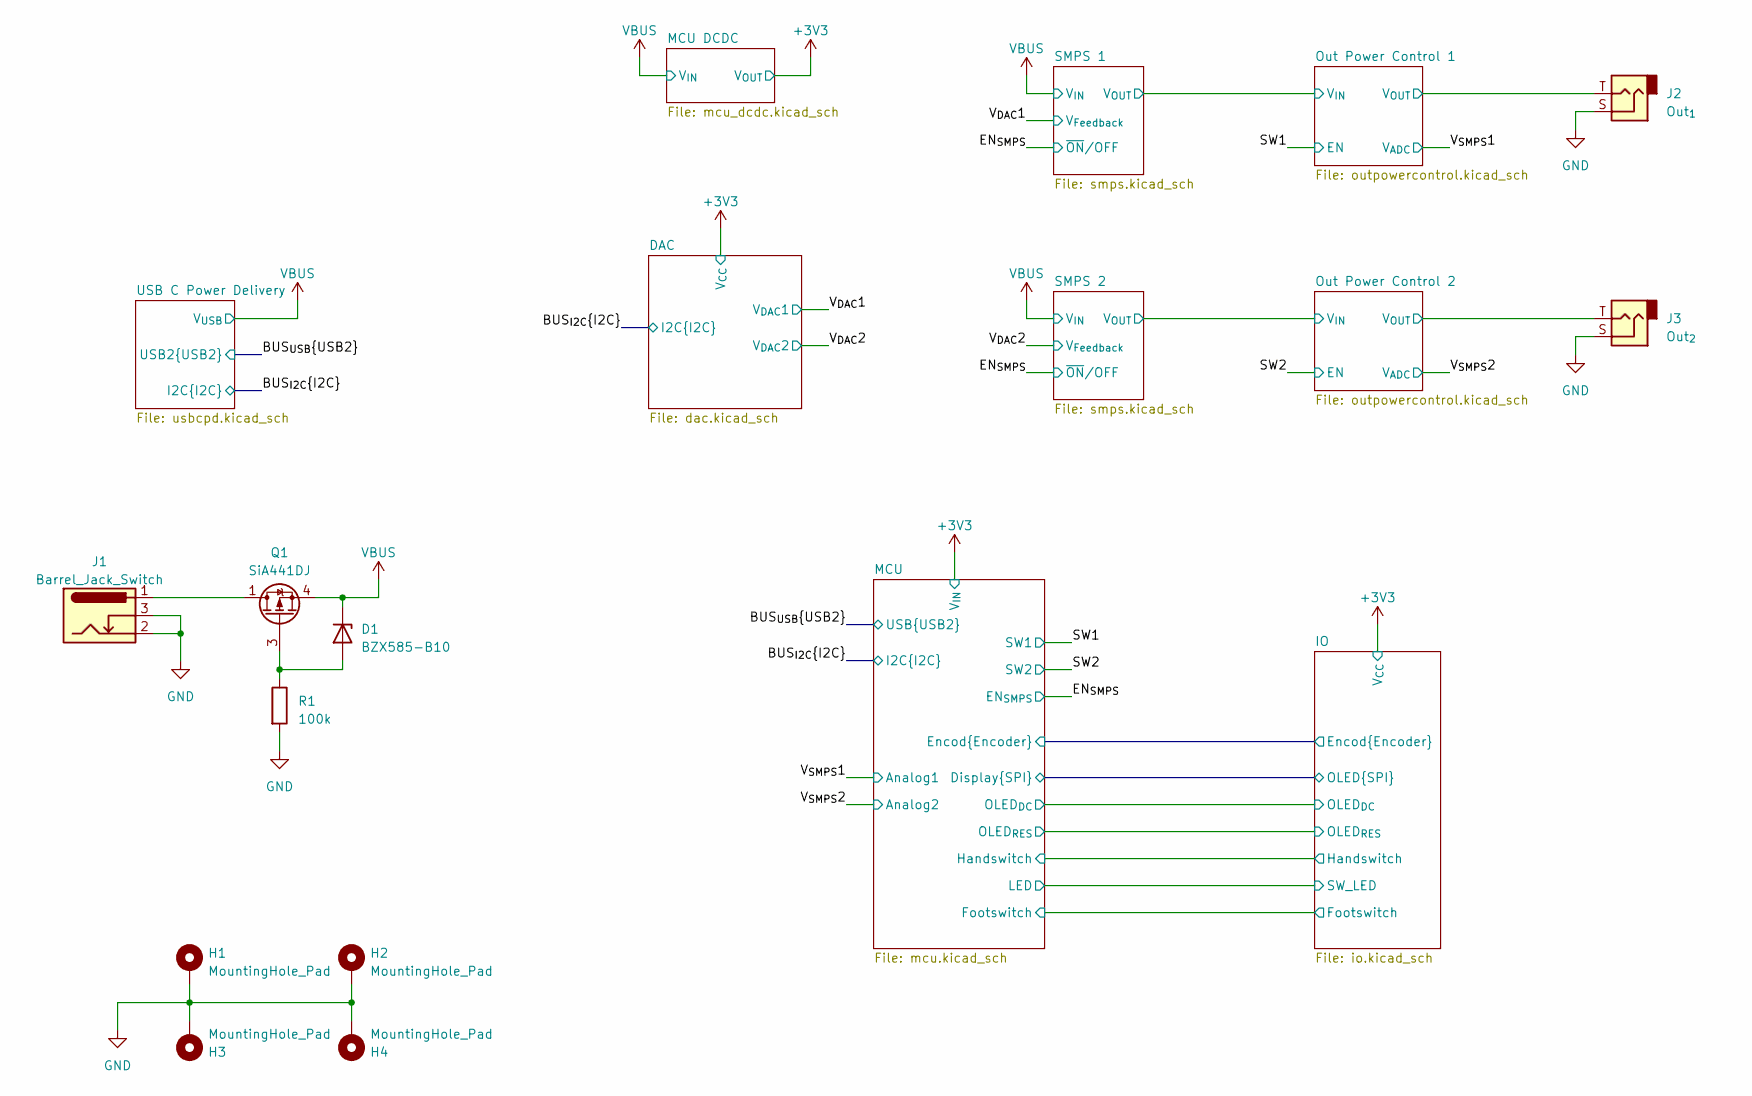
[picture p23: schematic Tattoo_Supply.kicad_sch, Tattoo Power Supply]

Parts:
D1: BZX585-B10; D_SOD-523; MPN BZX585-B10,135
H1, H2, H3, H4: MountingHole_Pad; MountingHole_2.7mm_M2.5_DIN965_Pad
J1: Barrel_Jack_Switch; BarrelJack_CUI_PJ-102AH_Horizontal; MPN PJ-102A
J2: Out_{1}; MJ63022A; MPN MJ-63022A
J3: Out_{2}; MJ63022A; MPN MJ-63022A
Q1: SiA441DJ; Vishay_PowerPAK_SC70-6L_Single; MPN SIA441DJ-T1-GE3
R1: 100k; R_0603_1608Metric; MPN ERJ-3EKF1003V

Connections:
/Out Power Control 1/V_{OUT}: J2.T; also elsewhere on the board
/Out Power Control 2/V_{OUT}: J3.T; also elsewhere on the board
GND: H1.1, H2.1, H3.1, H4.1, J1.2, J1.3, J2.S, J3.S, R1.2; also elsewhere on the board
unnamed: D1.2 (A), Q1.3 (G), R1.1
unnamed: J1.1, Q1.1 (D)
VBUS: D1.1 (K), Q1.4 (S); also elsewhere on the board

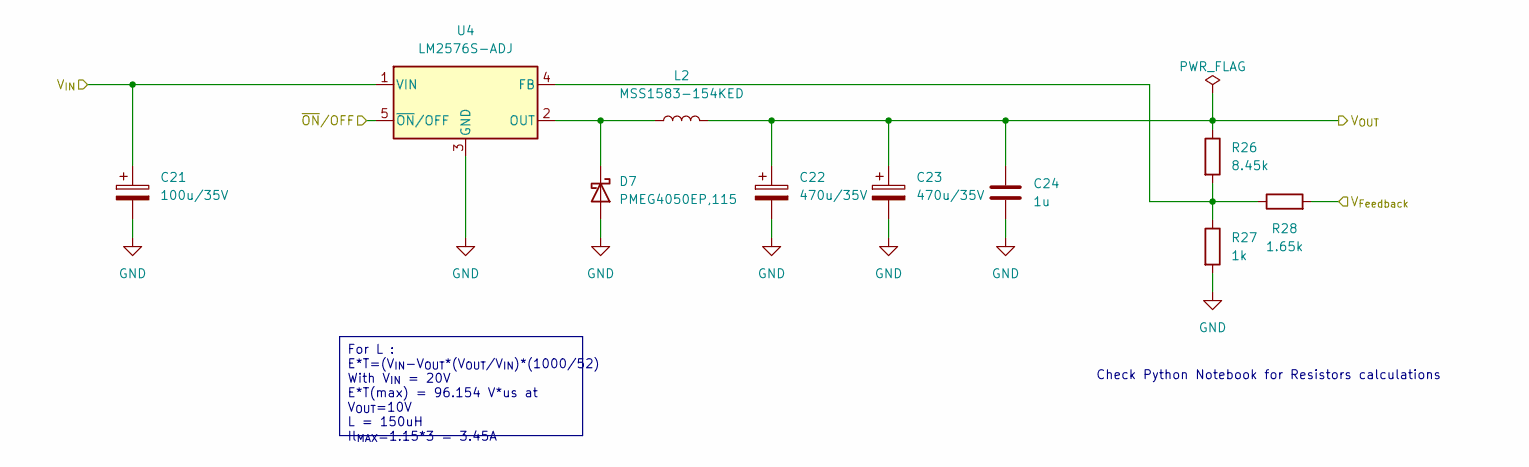
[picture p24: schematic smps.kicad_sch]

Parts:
C21: 100u/35V; CP_Elec_6.3x7.7; MPN 865080545012
C22, C23: 470u/35V; CP_Elec_8x10; MPN EMZS350ARA471MHA0G
C24: 1u; C_0603_1608Metric; MPN CGA3E1X7R1V105K080AC
D7: PMEG4050EP,115; D_SOD-128; MPN PMEG4050EP,115
L2: MSS1583-154KED; MSS1583; MPN MSS1583-154KED
R26: 8.45k; R_0603_1608Metric; MPN ERJ-3EKF8451V
R27: 1k; R_0603_1608Metric; MPN ERJ-3EKF1001V
R28: 1.65k; R_0603_1608Metric; MPN ERJ-3EKF1651V
U4: LM2576S-ADJ; TO-263-5_TabPin3; MPN LM2576D2T-ADJR4G

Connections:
/EN_{SMPS}: U4.5 (~ON/OFF); also elsewhere on the board
/Out Power Control 1/V_{IN}: C22.1, C23.1, C24.1, L2.2, R26.1; also elsewhere on the board
/V_{DAC}1: R28.2; also elsewhere on the board
GND: C21.2, C22.2, C23.2, C24.2, D7.2 (A), R27.2, U4.3 (GND); also elsewhere on the board
unnamed: D7.1 (K), L2.1, U4.2 (OUT)
unnamed: R26.2, R27.1, R28.1, U4.4 (FB)
VBUS: C21.1, U4.1 (VIN); also elsewhere on the board

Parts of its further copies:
C7: 100u/35V; CP_Elec_6.3x7.7; MPN 865080545012
C8, C9: 470u/35V; CP_Elec_8x10; MPN EMZS350ARA471MHA0G
C10: 1u; C_0603_1608Metric; MPN CGA3E1X7R1V105K080AC
D6: PMEG4050EP,115; D_SOD-128; MPN PMEG4050EP,115
L1: MSS1583-154KED; MSS1583; MPN MSS1583-154KED
R13: 8.45k; R_0603_1608Metric; MPN ERJ-3EKF8451V
R14: 1k; R_0603_1608Metric; MPN ERJ-3EKF1001V
R15: 1.65k; R_0603_1608Metric; MPN ERJ-3EKF1651V
U2: LM2576S-ADJ; TO-263-5_TabPin3; MPN LM2576D2T-ADJR4G

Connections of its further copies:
/EN_{SMPS}: U2.5 (~ON/OFF); also elsewhere on the board
/Out Power Control 2/V_{IN}: C8.1, C9.1, C10.1, L1.2, R13.1; also elsewhere on the board
/V_{DAC}2: R15.2; also elsewhere on the board
GND: C7.2, C8.2, C9.2, C10.2, D6.2 (A), R14.2, U2.3 (GND); also elsewhere on the board
unnamed: D6.1 (K), L1.1, U2.2 (OUT)
unnamed: R13.2, R14.1, R15.1, U2.4 (FB)
VBUS: C7.1, U2.1 (VIN); also elsewhere on the board

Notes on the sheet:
For L : E*T=(V_{IN}-V_{OUT}*(V_{OUT}/V_{IN})*(1000/52) With V_{IN} = 20V E*T(max) = 96.154 V*us at V_{OUT}=10V L = 150uH Il_{MAX}=1.15*3 = 3.45A
Check Python Notebook for Resistors calculations

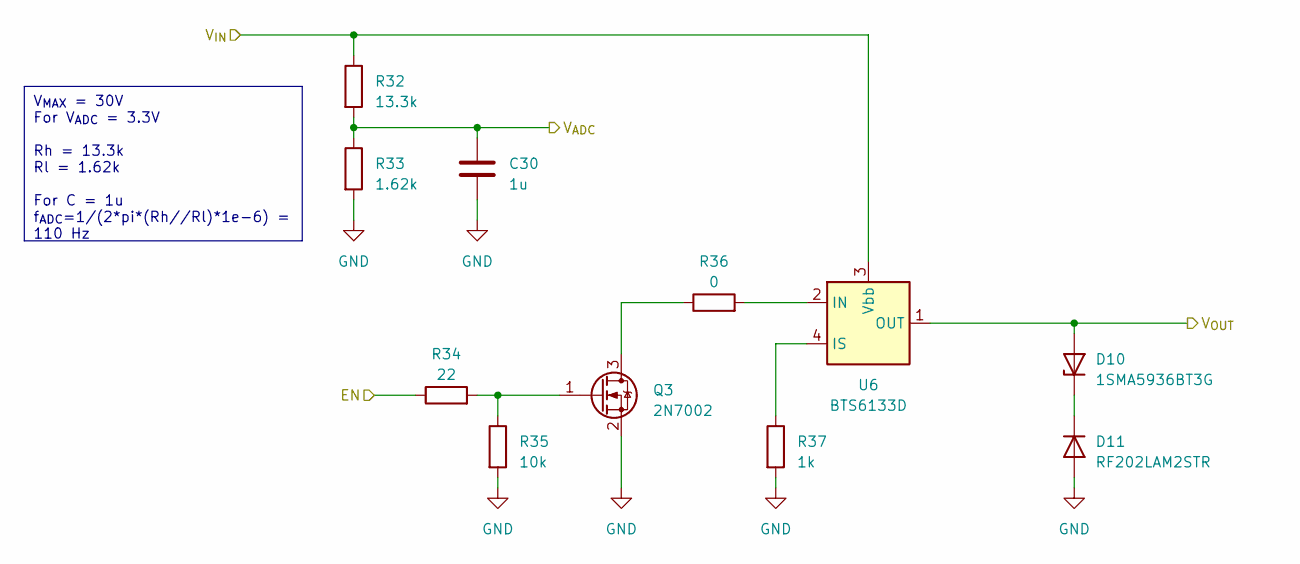
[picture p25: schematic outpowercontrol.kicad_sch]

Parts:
C30: 1u; C_0603_1608Metric; MPN CGA3E1X7R1V105K080AC
D10: 1SMA5936BT3G; D_SMA; MPN 1SMA5936BT3G
D11: RF202LAM2STR; D_SOD-128; MPN RF202LAM2STR
Q3: 2N7002; SOT-23; MPN 2N7002NXAKR
R32: 13.3k; R_0603_1608Metric; MPN ERJ-3EKF1332V
R33: 1.62k; R_0603_1608Metric; MPN ERJ-3EKF1621V
R34: 22; R_0603_1608Metric; MPN ERJ-3EKF22R0V
R35: 10k; R_0603_1608Metric; MPN ERJ-3EKF1002V
R36: 0; R_0603_1608Metric; MPN ERJ-3GEY0R00V
R37: 1k; R_0603_1608Metric; MPN ERJ-3EKF1001V
U6: BTS6133D; TO-252-4; MPN BTS6133D

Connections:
/Out Power Control 1/V_{IN}: R32.1, U6.3 (Vbb); also elsewhere on the board
/Out Power Control 1/V_{OUT}: D10.2 (A), U6.1 (OUT), U6.5 (OUT); also elsewhere on the board
/SW1: R34.1; also elsewhere on the board
/V_{SMPS}1: C30.1, R32.2, R33.1; also elsewhere on the board
GND: C30.2, D11.2 (A), Q3.2 (S), R33.2, R35.2, R37.2; also elsewhere on the board
unnamed: D10.1 (K), D11.1 (K)
unnamed: Q3.3 (D), R36.1
unnamed: Q3.1 (G), R34.2, R35.1
unnamed: R36.2, U6.2 (IN)
unnamed: R37.1, U6.4 (IS)

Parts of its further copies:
C34: 1u; C_0603_1608Metric; MPN CGA3E1X7R1V105K080AC
D12: 1SMA5936BT3G; D_SMA; MPN 1SMA5936BT3G
D13: RF202LAM2STR; D_SOD-128; MPN RF202LAM2STR
Q4: 2N7002; SOT-23; MPN 2N7002NXAKR
R42: 13.3k; R_0603_1608Metric; MPN ERJ-3EKF1332V
R43: 1.62k; R_0603_1608Metric; MPN ERJ-3EKF1621V
R44: 22; R_0603_1608Metric; MPN ERJ-3EKF22R0V
R45: 10k; R_0603_1608Metric; MPN ERJ-3EKF1002V
R46: 0; R_0603_1608Metric; MPN ERJ-3GEY0R00V
R47: 1k; R_0603_1608Metric; MPN ERJ-3EKF1001V
U8: BTS6133D; TO-252-4; MPN BTS6133D

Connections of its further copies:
/Out Power Control 2/V_{IN}: R42.1, U8.3 (Vbb); also elsewhere on the board
/Out Power Control 2/V_{OUT}: D12.2 (A), U8.1 (OUT), U8.5 (OUT); also elsewhere on the board
/SW2: R44.1; also elsewhere on the board
/V_{SMPS}2: C34.1, R42.2, R43.1; also elsewhere on the board
GND: C34.2, D13.2 (A), Q4.2 (S), R43.2, R45.2, R47.2; also elsewhere on the board
unnamed: D12.1 (K), D13.1 (K)
unnamed: Q4.3 (D), R46.1
unnamed: Q4.1 (G), R44.2, R45.1
unnamed: R46.2, U8.2 (IN)
unnamed: R47.1, U8.4 (IS)

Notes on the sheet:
V_{MAX} = 30V For V_{ADC} = 3.3V Rh = 13.3k Rl = 1.62k For C = 1u f_{ADC}=1/(2*pi*(Rh//Rl)*1e-6) = 110 Hz

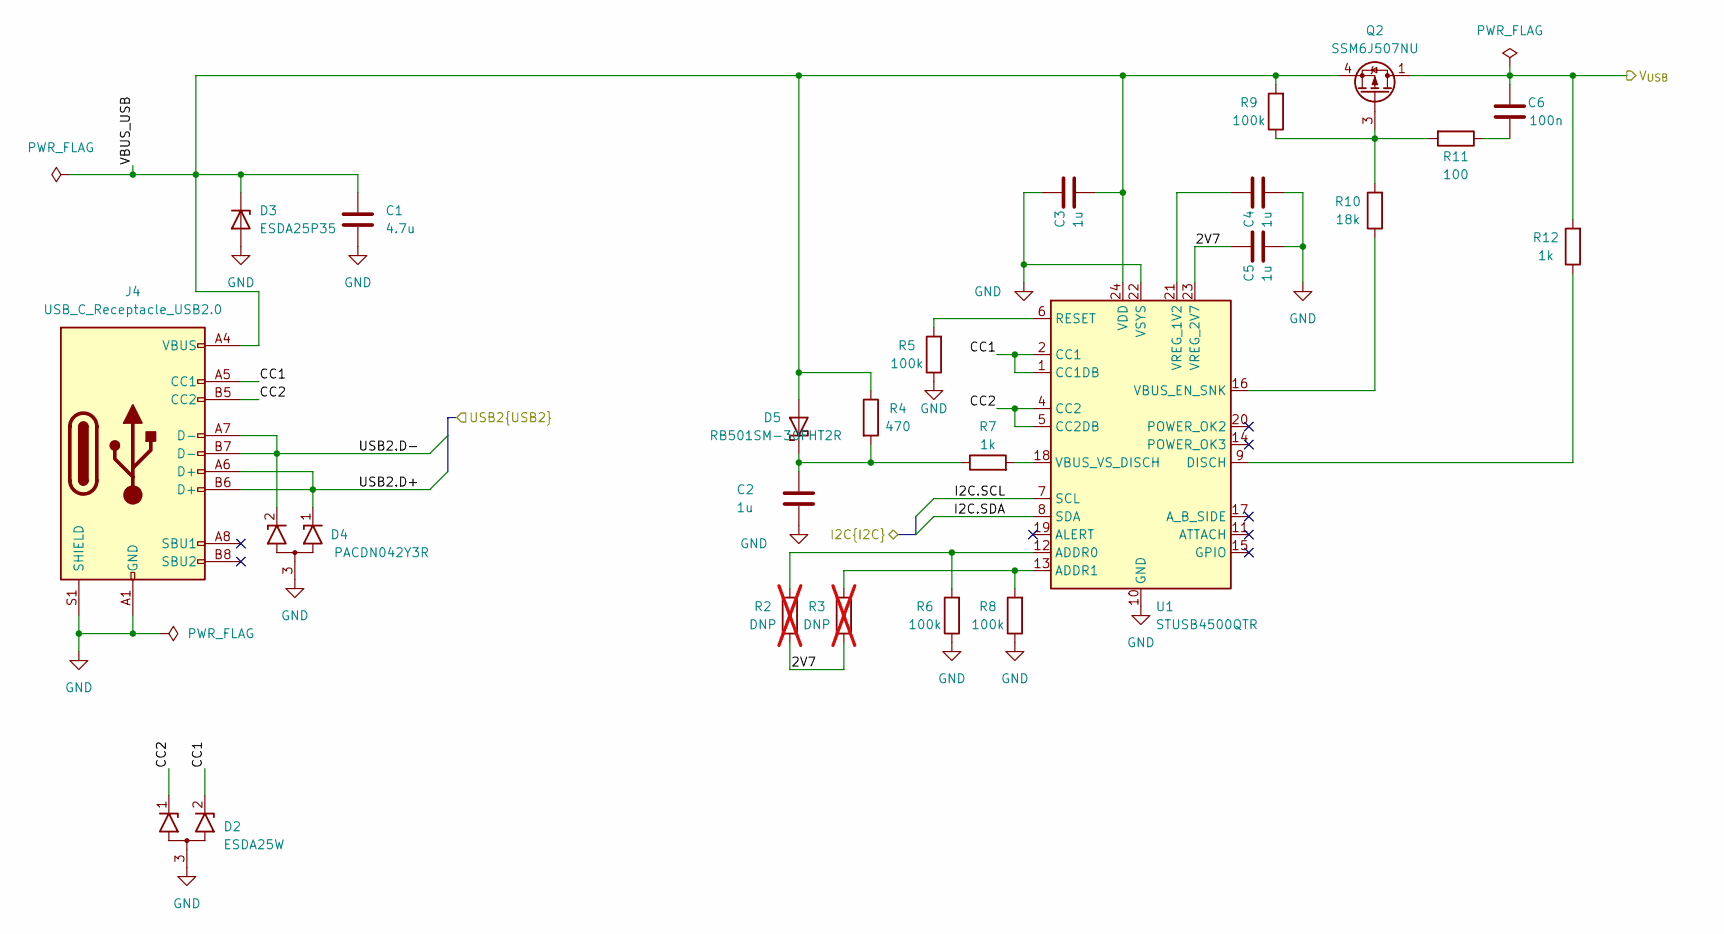
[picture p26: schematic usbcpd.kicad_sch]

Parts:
C1: 4.7u; C_0805_2012Metric; MPN GRM219R6YA475KA73D
C2, C3, C4, C5: 1u; C_0603_1608Metric; MPN CGA3E1X7R1V105K080AC
C6: 100n; C_0603_1608Metric; MPN CGA3E2X7R1H104M080AA
D2: ESDA25W; SOT-323_SC-70; MPN ESDA25W
D3: ESDA25P35; D_0603_1608Metric; MPN ESDA25P35-1U1M
D4: PACDN042Y3R; SOT-23-3; MPN PACDN042Y3R
D5: RB501SM-30FHT2R; D_SOD-523; MPN RB501SM-30FHT2R
J4: USB_C_Receptacle_USB2.0; USB_C_Receptacle_GCT_USB4105-xx-A_16P_TopMnt_Horizontal; MPN GCT
Q2: SSM6J507NU; TRANS_SSM6J507NU,LF; MPN SSM6J507NU
R2, R3: DNP; R_0603_1608Metric; not fitted
R4: 470; R_0603_1608Metric; MPN ERJ-3EKF4700V
R5, R6, R8, R9: 100k; R_0603_1608Metric; MPN ERJ-3EKF1003V
R7, R12: 1k; R_0603_1608Metric; MPN ERJ-3EKF1001V
R10: 18k; R_0603_1608Metric; MPN ERJ-3EKF1802V
R11: 100; R_0603_1608Metric; MPN ERJ-3EKF1000V
U1: STUSB4500QTR; QFN-24-1EP_4x4mm_P0.5mm_EP2.7x2.7mm; MPN STUSB4500QTR

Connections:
/BUS_{I2C}.SCL: U1.7 (SCL); also elsewhere on the board
/BUS_{I2C}.SDA: U1.8 (SDA); also elsewhere on the board
/BUS_{USB}.D+: D4.1 (K1), J4.A6 (D+), J4.B6 (D+); also elsewhere on the board
/BUS_{USB}.D-: D4.2 (K2), J4.A7 (D-), J4.B7 (D-); also elsewhere on the board
/USB C Power Delivery/2V7: C5.1, R2.1, R3.1, U1.23 (VREG_2V7)
/USB C Power Delivery/CC1: D2.2 (K2), J4.A5 (CC1), U1.1 (CC1DB), U1.2 (CC1)
/USB C Power Delivery/CC2: D2.1 (K1), J4.B5 (CC2), U1.4 (CC2), U1.5 (CC2DB)
/USB C Power Delivery/VBUS_USB: C1.1, C3.2, D3.1 (K), D5.2 (A), J4.A4 (VBUS), J4.A9 (VBUS), J4.B4 (VBUS), J4.B9 (VBUS), Q2.4 (S), Q2.8 (S), R4.1, R9.2, U1.24 (VDD)
GND: C1.2, C2.2, C3.1, C4.2, C5.2, D2.3 (A), D3.2 (A), D4.3 (A), J4.A1 (GND), J4.A12 (GND), J4.B1 (GND), J4.B12 (GND), J4.S1 (SHIELD), R5.1, R6.1, R8.1, U1.10 (GND), U1.22 (VSYS), U1.25 (GND); also elsewhere on the board
unnamed: C6.1, R11.1
unnamed: C2.1, D5.1 (K), R4.2, R7.1
unnamed: Q2.3 (G), R9.1, R10.2, R11.2
unnamed: R2.2, R6.2, U1.12 (ADDR0)
unnamed: R3.2, R8.2, U1.13 (ADDR1)
unnamed: R12.1, U1.9 (DISCH)
unnamed: R5.2, U1.6 (RESET)
unnamed: R10.1, U1.16 (VBUS_EN_SNK)
unnamed: R7.2, U1.18 (VBUS_VS_DISCH)
unnamed: C4.1, U1.21 (VREG_1V2)
VBUS: C6.2, Q2.1 (D), Q2.2 (D), Q2.5 (D), Q2.6 (D), Q2.7 (D), R12.2; also elsewhere on the board

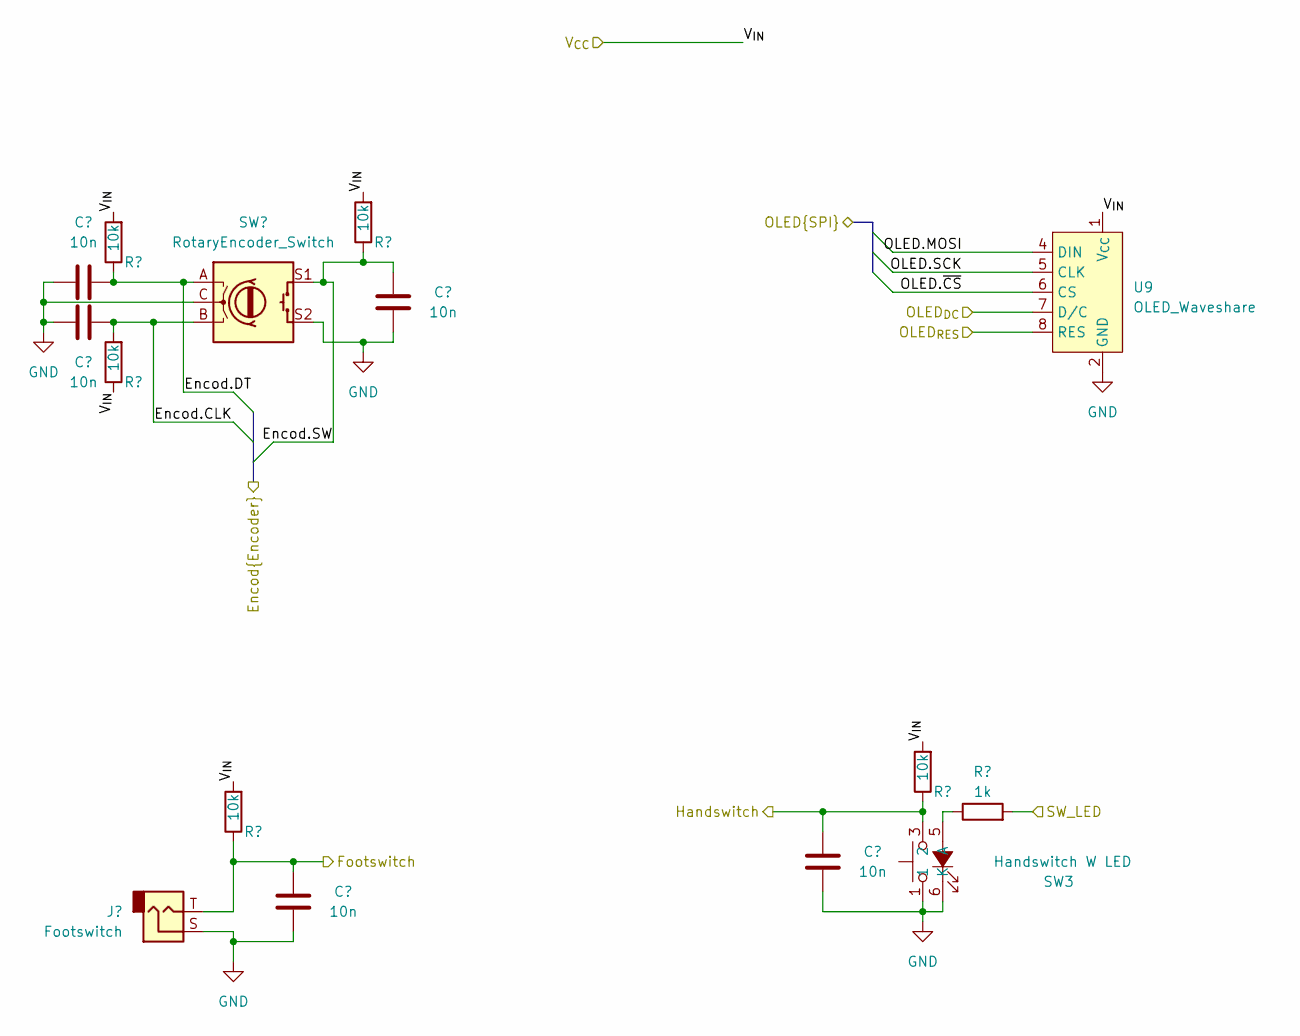
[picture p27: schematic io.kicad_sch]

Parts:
C35, C36, C37, C38, C39: 10n; C_0603_1608Metric; MPN GCM188R71H103KA37J
J8: Footswitch; MJ63022A; MPN MJ-63022A
R48, R49, R50, R51, R52: 10k; R_0603_1608Metric; MPN ERJ-3EKF1002V
R53: 1k; R_0603_1608Metric; MPN ERJ-3EKF1001V
SW2: RotaryEncoder_Switch; RotaryEncoder_Alps_EC11E-Switch_Vertical_H20mm; MPN PEC11R-4220F-S0024
SW3: Handswitch W LED; D6RLxx; MPN D6RLRDF1 LFS
U9: OLED_Waveshare; OLEDs_Waveshare_4SPI; MPN Waveshare

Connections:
+3V3: R48.2, R49.1, R50.2, R51.2, R52.2, U9.1 (V_{CC}); also elsewhere on the board
/IO/Encod.CLK: C36.1, R49.2, SW2.B; also elsewhere on the board
/IO/Encod.DT: C35.2, R48.1, SW2.A; also elsewhere on the board
/IO/Encod.SW: C38.1, R51.1, SW2.S1; also elsewhere on the board
/IO/Footswitch: C37.1, J8.T, R50.1; also elsewhere on the board
/IO/Handswitch: C39.1, R52.1, SW3.3 (2), SW3.4 (2); also elsewhere on the board
/IO/OLED.MOSI: U9.4 (DIN); also elsewhere on the board
/IO/OLED.SCK: U9.5 (CLK); also elsewhere on the board
/IO/OLED.~CS: U9.6 (CS); also elsewhere on the board
/IO/OLED_{DC}: U9.7 (D/C); also elsewhere on the board
/IO/OLED_{RES}: U9.8 (RES); also elsewhere on the board
/IO/SW_LED: R53.2; also elsewhere on the board
GND: C35.1, C36.2, C37.2, C38.2, C39.2, J8.S, SW2.C, SW2.S2, SW3.1, SW3.2 (1), SW3.6 (K), U9.2 (GND); also elsewhere on the board
unnamed: R53.1, SW3.5 (A)

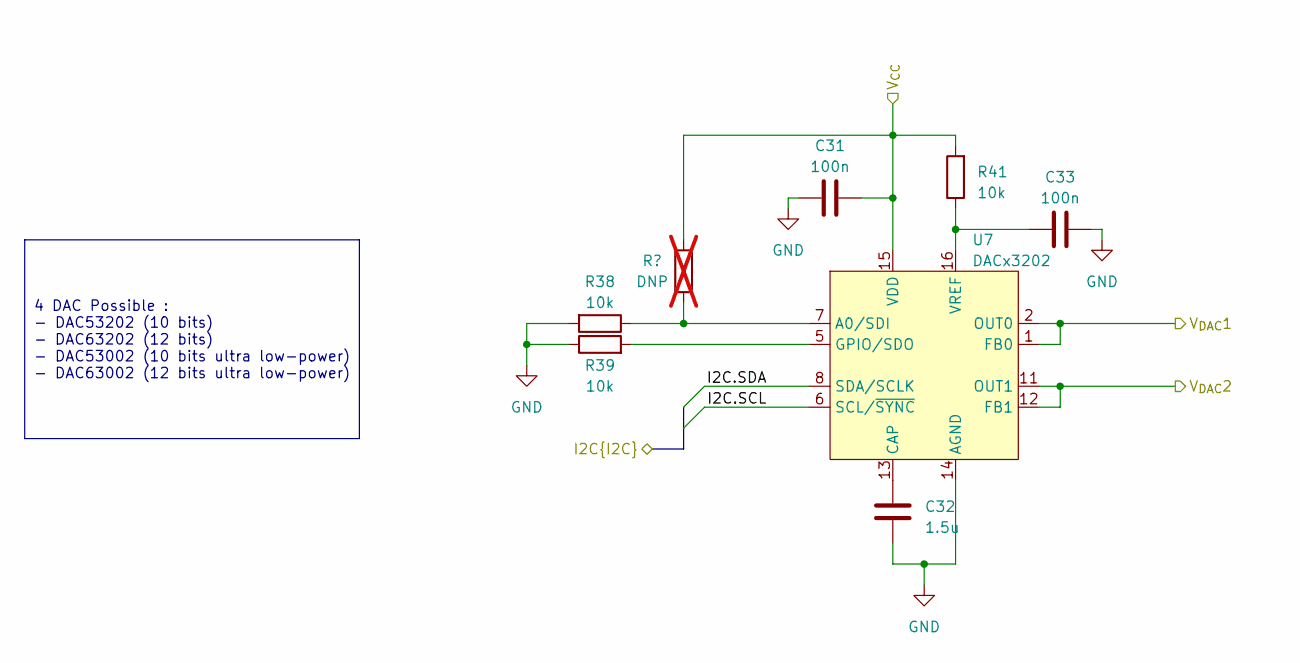
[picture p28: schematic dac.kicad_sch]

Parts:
C31, C33: 100n; C_0603_1608Metric; MPN CGA3E2X7R1H104M080AA
C32: 1.5u; C_0603_1608Metric; MPN C1608X7R1A155K080AC
R38, R39, R41: 10k; R_0603_1608Metric; MPN ERJ-3EKF1002V
R40: DNP; R_0603_1608Metric; not fitted
U7: DACx3202; WQFN-16-1EP_3x3mm_P0.5mm_EP1.68x1.68mm; MPN DAC63202RTER

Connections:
+3V3: C31.2, R40.2, R41.2, U7.15 (VDD); also elsewhere on the board
/BUS_{I2C}.SCL: U7.6 (SCL/~SYNC); also elsewhere on the board
/BUS_{I2C}.SDA: U7.8 (SDA/SCLK); also elsewhere on the board
/V_{DAC}1: U7.1 (FB0), U7.2 (OUT0); also elsewhere on the board
/V_{DAC}2: U7.11 (OUT1), U7.12 (FB1); also elsewhere on the board
GND: C31.1, C32.2, C33.2, R38.2, R39.1, U7.14 (AGND), U7.17 (AGND); also elsewhere on the board
unnamed: R38.1, R40.1, U7.7 (A0/SDI)
unnamed: C32.1, U7.13 (CAP)
unnamed: R39.2, U7.5 (GPIO/SDO)
unnamed: C33.1, R41.1, U7.16 (VREF)

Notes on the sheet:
4 DAC Possible : - DAC53202 (10 bits) - DAC63202 (12 bits) - DAC53002 (10 bits ultra low-power) - DAC63002 (12 bits ultra low-power)

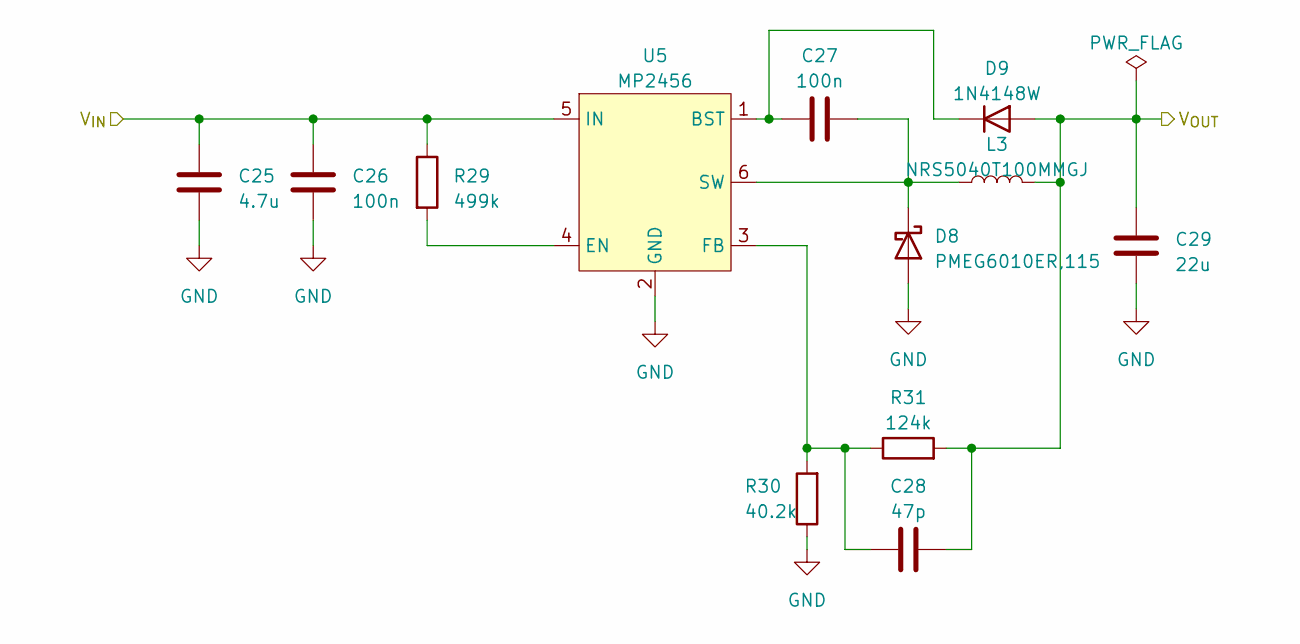
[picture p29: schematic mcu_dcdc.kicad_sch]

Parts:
C25: 4.7u; C_0805_2012Metric; MPN GRM219R6YA475KA73D
C26, C27: 100n; C_0603_1608Metric; MPN CGA3E2X7R1H104M080AA
C28: 47p; C_0603_1608Metric; MPN C1608C0G1H470J080AA
C29: 22u; C_0805_2012Metric; MPN GRM21BC81C226ME44L
D8: PMEG6010ER,115; D_SOD-123F; MPN PMEG6010ER,115
D9: 1N4148W; D_SOD-123; MPN 1N4148W-7-F
L3: NRS5040T100MMGJ; L_Taiyo-Yuden_NR-50xx; MPN NRS5040T100MMGJ
R29: 499k; R_0603_1608Metric; MPN ERJ-3EKF4993V
R30: 40.2k; R_0603_1608Metric; MPN ERJ-3EKF4022V
R31: 124k; R_0603_1608Metric; MPN ERJ-3EKF1243V
U5: MP2456; TSOT-23-6; MPN MP2456GJ-Z

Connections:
+3V3: C28.2, C29.1, D9.2 (A), L3.2, R31.2; also elsewhere on the board
GND: C25.2, C26.2, C29.2, D8.2 (A), R30.1, U5.2 (GND); also elsewhere on the board
unnamed: C27.2, D8.1 (K), L3.1, U5.6 (SW)
unnamed: C27.1, D9.1 (K), U5.1 (BST)
unnamed: R29.2, U5.4 (EN)
unnamed: C28.1, R30.2, R31.1, U5.3 (FB)
VBUS: C25.1, C26.1, R29.1, U5.5 (IN); also elsewhere on the board

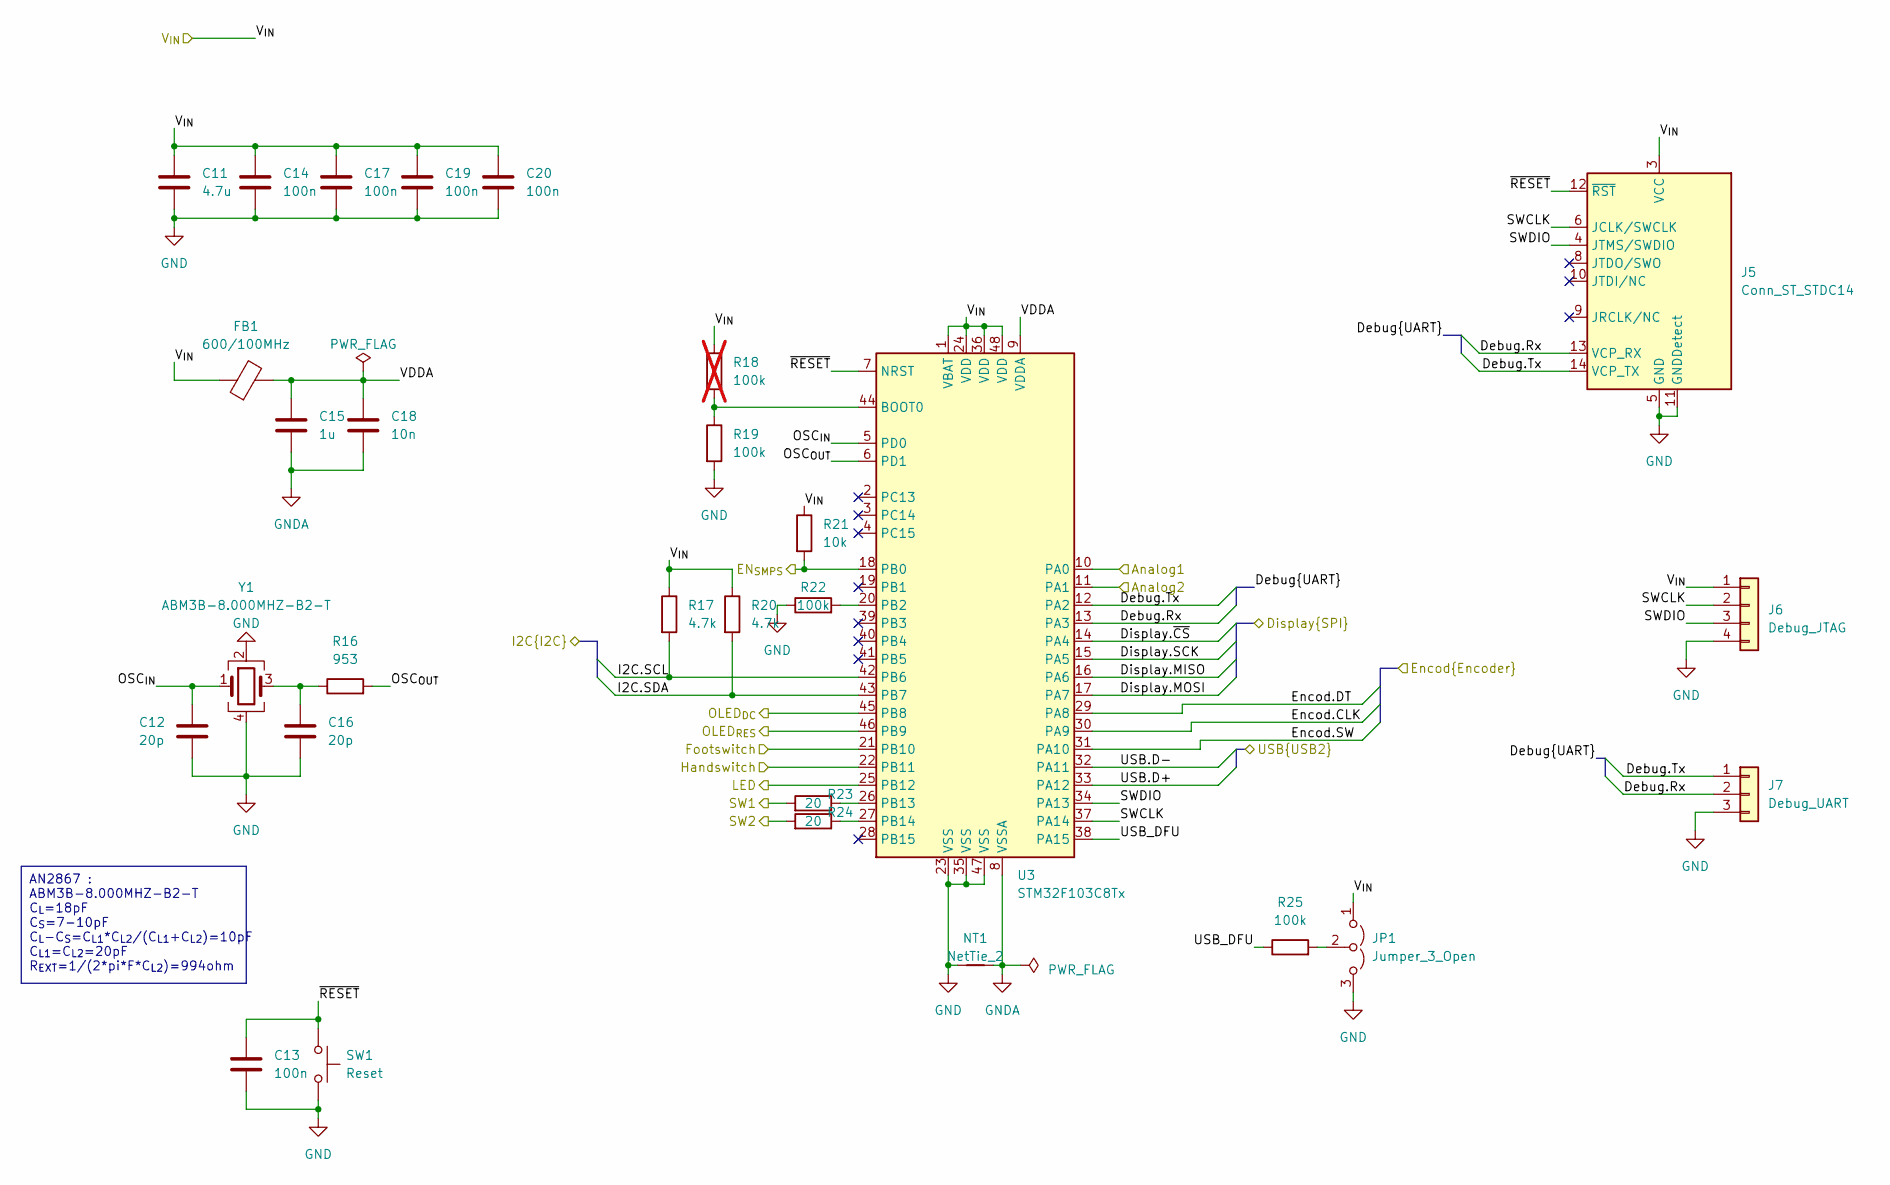
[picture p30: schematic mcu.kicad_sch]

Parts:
C11: 4.7u; C_0805_2012Metric; MPN GRM219R6YA475KA73D
C12, C16: 20p; C_0603_1608Metric; MPN C0603C200J5HACTU
C13, C14, C17, C19, C20: 100n; C_0603_1608Metric; MPN CGA3E2X7R1H104M080AA
C15: 1u; C_0603_1608Metric; MPN CGA3E1X7R1V105K080AC
C18: 10n; C_0603_1608Metric; MPN GCM188R71H103KA37J
FB1: 600/100MHz; R_0603_1608Metric; MPN 742792651
J5: Conn_ST_STDC14; PinHeader_2x07_P1.27mm_Vertical_SMD; MPN 20021121-00014C1LF
J6: Debug_JTAG; PinHeader_1x04_P2.54mm_Vertical
J7: Debug_UART; PinHeader_1x03_P2.54mm_Vertical
JP1: Jumper_3_Open; PinHeader_1x03_P2.54mm_Vertical
NT1: NetTie_2; NetTie-2_SMD_Pad0.5mm
R16: 953; R_0603_1608Metric; MPN ERJ-3EKF9530V
R17, R20: 4.7k; R_0603_1608Metric; MPN ERJ-3EKF4701V
R18: 100k; R_0603_1608Metric; MPN ERJ-3EKF1003V; not fitted
R19, R22, R25: 100k; R_0603_1608Metric; MPN ERJ-3EKF1003V
R21: 10k; R_0603_1608Metric; MPN ERJ-3EKF1002V
R23, R24: 20; R_0603_1608Metric; MPN ERJ-3EKF20R0V
SW1: Reset; SW_SPST_EVQP2; MPN EVQ-P2602W
U3: STM32F103C8Tx; LQFP-48_7x7mm_P0.5mm; MPN STM32F103C8T6
Y1: ABM3B-8.000MHZ-B2-T; Crystal_SMD_Abracon_ABM3B-4Pin_5.0x3.2mm; MPN ABM3B-8.000MHZ-B2-T

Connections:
+3V3: C11.1, C14.1, C17.1, C19.1, C20.1, FB1.1, J5.3 (VCC), J6.1, JP1.1 (A), R17.1, R18.1, R20.1, R21.1, U3.1 (VBAT), U3.24 (VDD), U3.36 (VDD), U3.48 (VDD); also elsewhere on the board
/BUS_{I2C}.SCL: R17.2, U3.42 (PB6); also elsewhere on the board
/BUS_{I2C}.SDA: R20.2, U3.43 (PB7); also elsewhere on the board
/BUS_{USB}.D+: U3.33 (PA12); also elsewhere on the board
/BUS_{USB}.D-: U3.32 (PA11); also elsewhere on the board
/EN_{SMPS}: R21.2, U3.18 (PB0); also elsewhere on the board
/IO/Encod.CLK: U3.30 (PA9); also elsewhere on the board
/IO/Encod.DT: U3.29 (PA8); also elsewhere on the board
/IO/Encod.SW: U3.31 (PA10); also elsewhere on the board
/IO/Footswitch: U3.21 (PB10); also elsewhere on the board
/IO/Handswitch: U3.22 (PB11); also elsewhere on the board
/IO/OLED.MISO: U3.16 (PA6)
/IO/OLED.MOSI: U3.17 (PA7); also elsewhere on the board
/IO/OLED.SCK: U3.15 (PA5); also elsewhere on the board
/IO/OLED.~CS: U3.14 (PA4); also elsewhere on the board
/IO/OLED_{DC}: U3.45 (PB8); also elsewhere on the board
/IO/OLED_{RES}: U3.46 (PB9); also elsewhere on the board
/IO/SW_LED: U3.25 (PB12); also elsewhere on the board
/MCU/Debug.Rx: J5.13 (VCP_RX), J7.2, U3.13 (PA3)
/MCU/Debug.Tx: J5.14 (VCP_TX), J7.1, U3.12 (PA2)
/MCU/OSC_{IN}: C12.1, U3.5 (PD0), Y1.1
/MCU/OSC_{OUT}: R16.2, U3.6 (PD1)
/MCU/SWCLK: J5.6 (JCLK/SWCLK), J6.2, U3.37 (PA14)
/MCU/SWDIO: J5.4 (JTMS/SWDIO), J6.3, U3.34 (PA13)
/MCU/USB_DFU: R25.1, U3.38 (PA15)
/MCU/VDDA: C15.1, C18.1, FB1.2, U3.9 (VDDA)
/MCU/~RESET: C13.1, J5.12 (~RST), SW1.1, U3.7 (NRST)
/SW1: R23.2; also elsewhere on the board
/SW2: R24.2; also elsewhere on the board
/V_{SMPS}1: U3.10 (PA0); also elsewhere on the board
/V_{SMPS}2: U3.11 (PA1); also elsewhere on the board
GND: C11.2, C12.2, C13.2, C14.2, C16.2, C17.2, C19.2, C20.2, J5.5 (GND), J5.7 (GND), J5.11 (GNDDetect), J6.4, J7.3, JP1.3 (B), NT1.2, R19.2, R22.1, SW1.2, U3.23 (VSS), U3.35 (VSS), U3.47 (VSS), Y1.2, Y1.4; also elsewhere on the board
GNDA: C15.2, C18.2, NT1.1, U3.8 (VSSA)
unnamed: C16.1, R16.1, Y1.3
unnamed: JP1.2 (C), R25.2
unnamed: R18.2, R19.1, U3.44 (BOOT0)
unnamed: R22.2, U3.20 (PB2)
unnamed: R23.1, U3.26 (PB13)
unnamed: R24.1, U3.27 (PB14)

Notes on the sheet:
AN2867 : ABM3B-8.000MHZ-B2-T C_{L}=18pF C_{S}=7-10pF C_{L}-C_{S}=C_{L1}*C_{L2}/(C_{L1}+C_{L2})=10pF C_{L1}=C_{L2}=20pF R_{EXT}=1/(2*pi*F*C_{L2})=994ohm

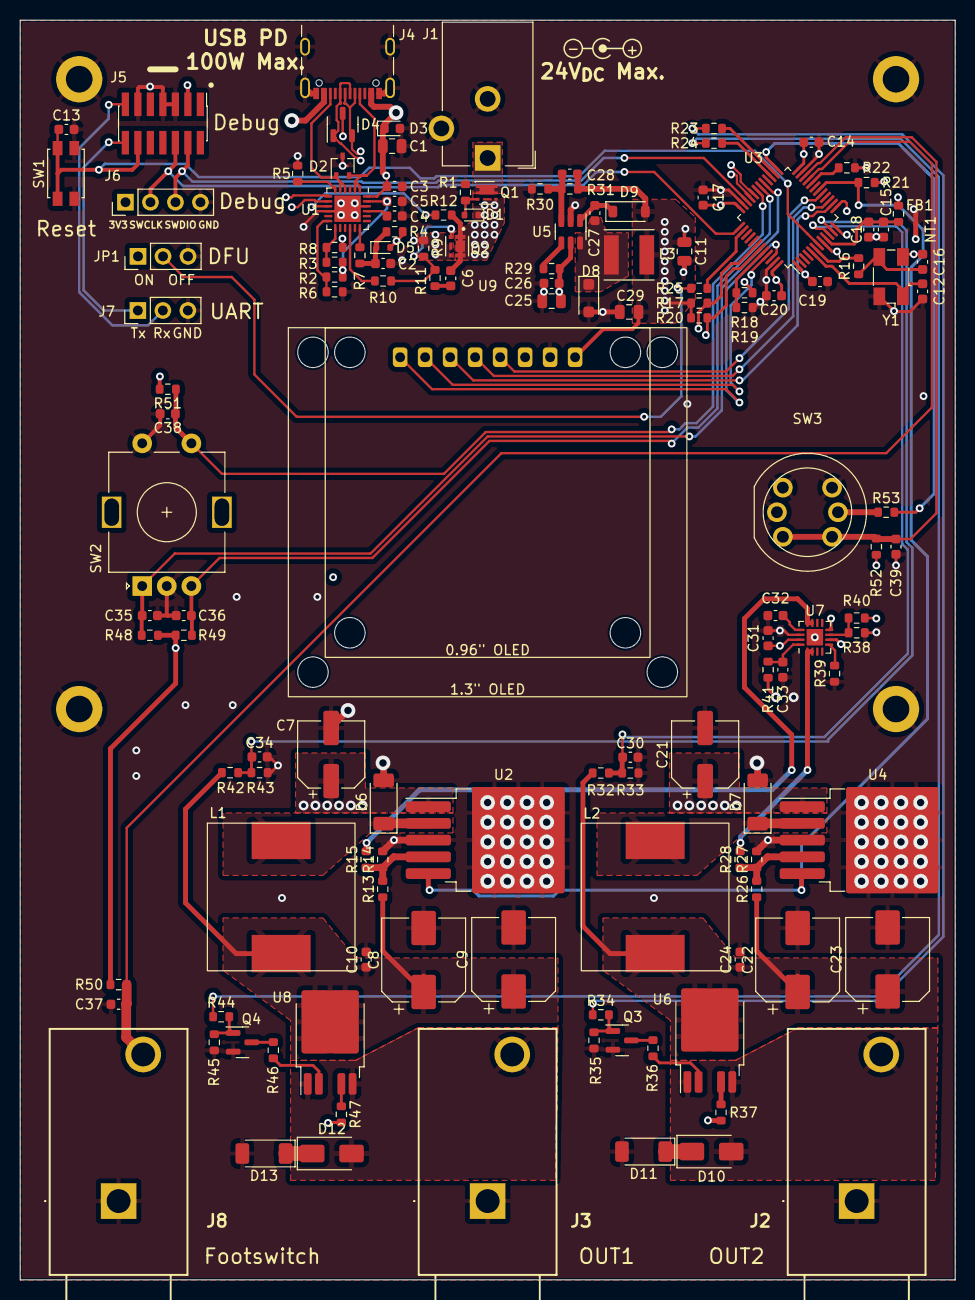
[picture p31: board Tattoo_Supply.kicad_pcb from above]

Board: 4 copper layers, 95.0 x 128.0 mm, 140 parts (0 on the bottom side), 84 nets.

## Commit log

2023-01-31 ok stm32
    [Tattoo_Supply.kicad_sch, mcu.kicad_sch]
2023-02-01 continue quartz
    [Tattoo_Supply.kicad_sch, mcu.kicad_sch]
2023-02-02 ok mcu
    [Tattoo_Supply.kicad_sch, mcu.kicad_sch, smps.kicad_sch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]
2023-02-03 DCDC almost done
    [Tattoo_Supply.kicad_sch, smps.kicad_sch]
2023-02-03 add mcu on off smps
    [Tattoo_Supply.kicad_sch, mcu.kicad_sch]
2023-02-04 almost ok stusb
    [Tattoo_Supply.kicad_sch, usbcpd.kicad_sch]
2023-02-09 update pin config stm32
    [Tattoo_Supply.kicad_sch, mcu.kicad_sch]
2023-02-15 upgrade usb protection + kicad 7
    [Tattoo_Supply.kicad_sch, ldo.kicad_sch, mcu.kicad_sch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]
2023-02-15 ok dcdc and power switches
    [Tattoo_Supply.kicad_sch, ldo.kicad_sch, mcu.kicad_sch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]
2023-02-16 add dac
    [Tattoo_Supply.kicad_sch, dac.kicad_sch, mcu.kicad_sch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]
2023-02-20 done with sch before ERC and footprints
    [Tattoo_Supply.kicad_pcb, Tattoo_Supply.kicad_sch, dac.kicad_sch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]
2023-02-26 begin BOM
    [Tattoo_Supply.kicad_sch, dac.kicad_sch, io.kicad_sch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]
2023-02-27 Resistors ok in BOM
    [Tattoo_Supply.kicad_sch, dac.kicad_sch, io.kicad_sch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]
2023-02-27 bom almost finished
    [Tattoo_Supply.kicad_sch, dac.kicad_sch, io.kicad_sch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]
2023-02-27 continue bom
    [Tattoo_Supply.kicad_sch, io.kicad_sch, usbcpd.kicad_sch]
2023-02-27 schematic done and bom ok
    [Tattoo_Supply.kicad_sch, Tattoo_Supply_bom_V1.0.csv, dac.kicad_sch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]
2023-02-28 add 3d models
    [Tattoo_Supply.kicad_pcb, Tattoo_Supply.kicad_sch, dac.kicad_sch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]
2023-03-01 ok better cap
    [Tattoo_Supply.kicad_pcb, Tattoo_Supply.kicad_sch, Tattoo_Supply_bom_V1.0.csv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]
2023-03-01 begin usb C
    [Tattoo_Supply.kicad_pcb]
2023-03-01 update dcdc 3V3 & begin routing
    [Tattoo_Supply.kicad_pcb, Tattoo_Supply.kicad_sch, mcu_dcdc.kicad_sch]
2023-03-05 first architecture
    [Tattoo_Supply.kicad_pcb]
2023-03-05 good second placement
    [Tattoo_Supply.kicad_pcb]
2023-03-06 placement ok
    [Tattoo_Supply.kicad_pcb, Tattoo_Supply.kicad_sch, mcu.kicad_sch]
2023-03-07 begin routing
    [Tattoo_Supply.kicad_pcb]
2023-03-07 routage en cours
    [Tattoo_Supply.kicad_pcb, Tattoo_Supply.kicad_sch, usbcpd.kicad_sch]
2023-03-08 ok route smps
    [Tattoo_Supply.kicad_pcb]
2023-03-10 routage ecran
    [Tattoo_Supply.kicad_pcb]
2023-03-12 almost done routing
    [Tattoo_Supply.kicad_pcb, Tattoo_Supply.kicad_sch, usbcpd.kicad_sch]
2023-03-13 done V1.0 + gerber + 3d
    [Tattoo_Supply.kicad_pcb]
2023-03-13 Release V1.0
    [Tattoo_Supply.kicad_pcb, Tattoo_Supply.kicad_sch]
2023-04-03 First drawing of the case
    [Case_V1.0.FCStd]
2023-05-05 Add calibration model
2023-05-07 add spreadsheet into freecad
    [Case_V1.0.FCStd]
2023-05-16 ok export case and spacer
    [Case_V1_bottom.3mf, Case_V1_top.3mf, Oled_Spacers.3mf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]
